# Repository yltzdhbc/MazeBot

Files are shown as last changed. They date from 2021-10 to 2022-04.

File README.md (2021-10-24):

> 📖 本项目更新于 2020 年 08 月 12 日

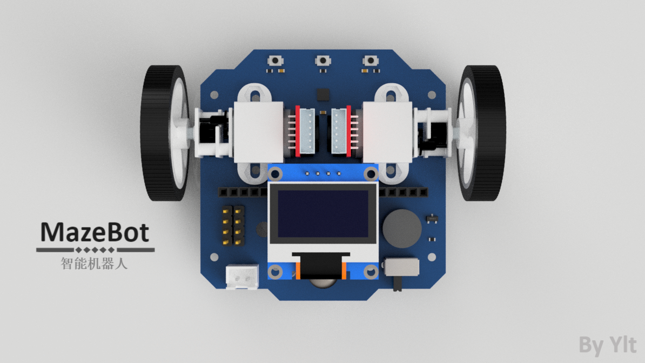
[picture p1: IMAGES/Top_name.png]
Mazebot v1 Top_name


MazeBot 始于2020年四月份，作为一个机器人研究者和爱好者，希望有一个硬件作为载体满足自己的软件的实验。

**我将持续更新该项目的进展**

### MazeBot的硬件资源：

| 元件 | 型号 | 说明 |
| --- | --- | :--- |
| 处理器 | STM32F405RGT6 | 160MHZ主频 DSP浮点加速 |
| 驱动器 | TB6612 | 双路直流电机驱动器 |
| 通讯 | ESP07S | 安信可WiFi芯片 |
| 电机 | N20 | 带正交编码器的直流有刷减速电机 |
| 陀螺仪 | mpu9250 | invensense的9轴姿态传感器 |
| 光电传感器 | ITR8307 | 收发一体的反射式光电传感器 |
| 显示器 | 0.96oled | SSD1306白黑oled |

<!-- more -->

### MazeBot能够用来干什么呢：

- 首先作为一个双轮差速的小车，能够提供最高1m/s的移动速度；
- 通过直流电机编码器反馈与mpu9250陀螺仪信息融合获得可靠的里程计信息；
- 前置五个光电传感器实现巡线学习；
- oled与三个操作按键进行人机交互；
- WiFi与上位机相连获取信息与控制；

---

### 我准备MazeBot做什么：

- 使用OPEN AI 训练其进行巡线；
- 使用模型优化轨迹跟踪算法的参数；

---

### 现在MazeBot完成了哪些部分：

- 电机速度闭环与位置闭环；
- 陀螺仪读取与矫正；
- 基于编码器与陀螺仪的里程计；
- Wifi AP模式和Station模式与上位机通信；
- 光电传感器对白线与黑线的识别；
- 轨迹规划与跟踪算法；

---

### 原理图和PCB

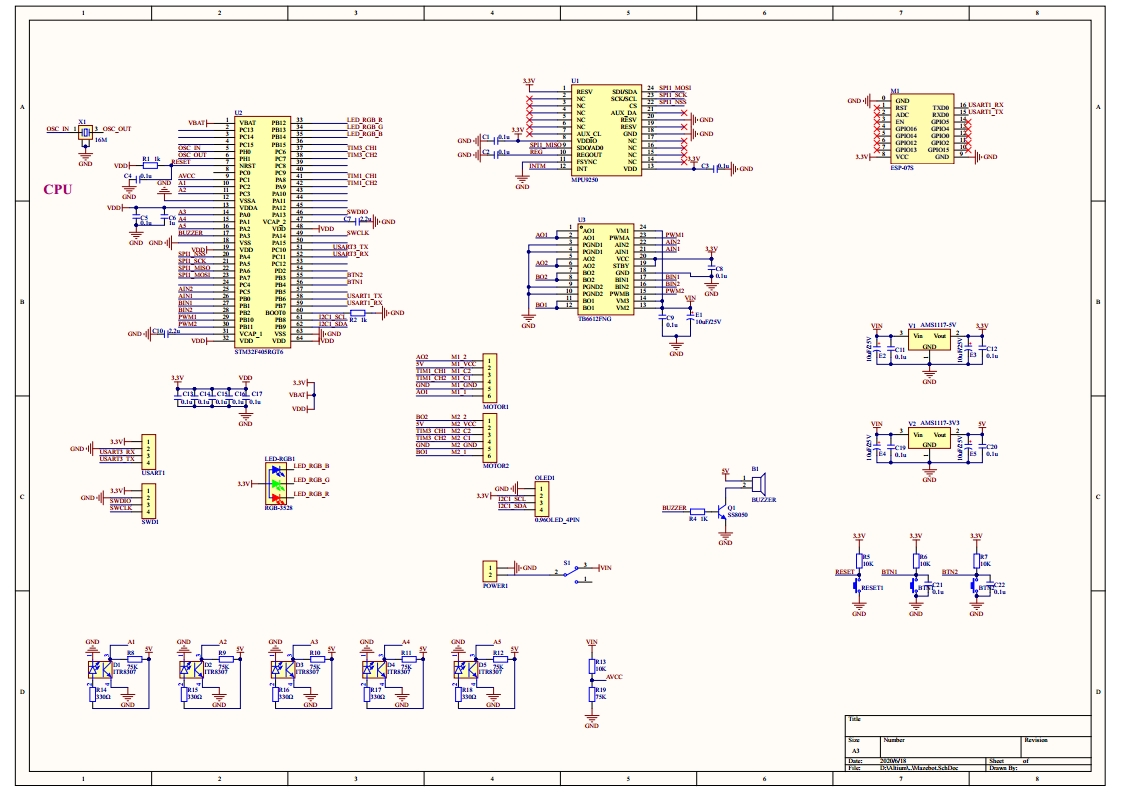
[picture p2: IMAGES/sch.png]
sch


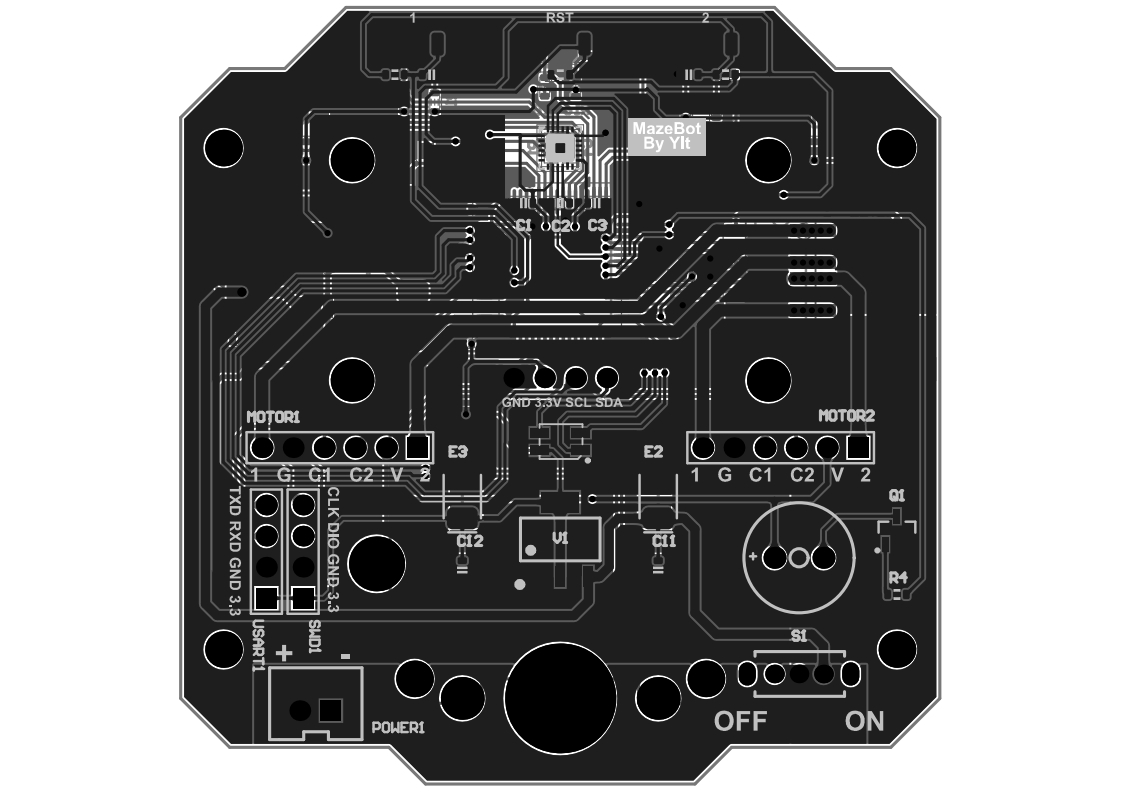
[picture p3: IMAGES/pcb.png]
pcb


### 渲染图

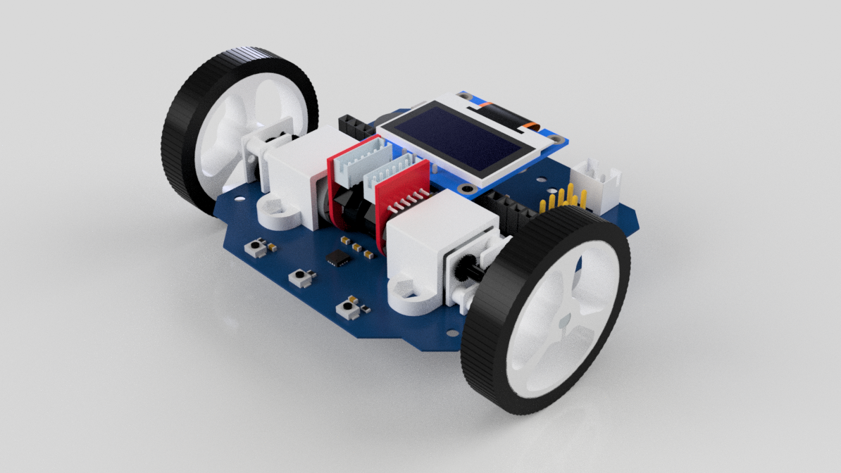
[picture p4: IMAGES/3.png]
Mazebot v2 3


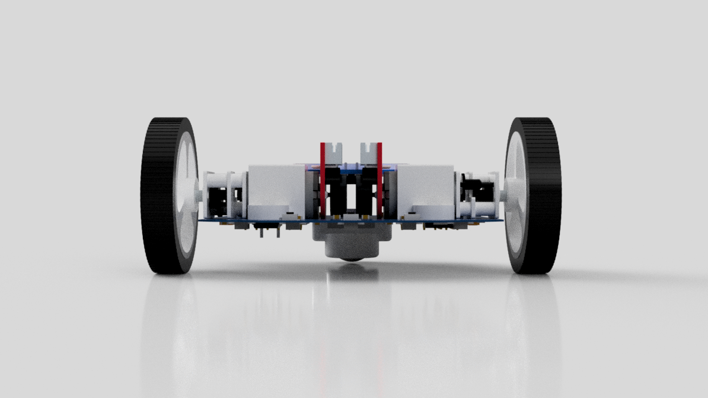
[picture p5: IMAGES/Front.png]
Mazebot v1 Front


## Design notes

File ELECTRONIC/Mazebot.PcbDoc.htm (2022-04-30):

Reporting Options

# File in Previous Format

Date | : | 2022/4/17
Time | : | 14:44:59
Filename | : | C:\UserData\Git\my_github\MazeBot\ELECTRONIC\Mazebot.PcbDoc

Version | Warning

This file was generated by an earlier version of the software

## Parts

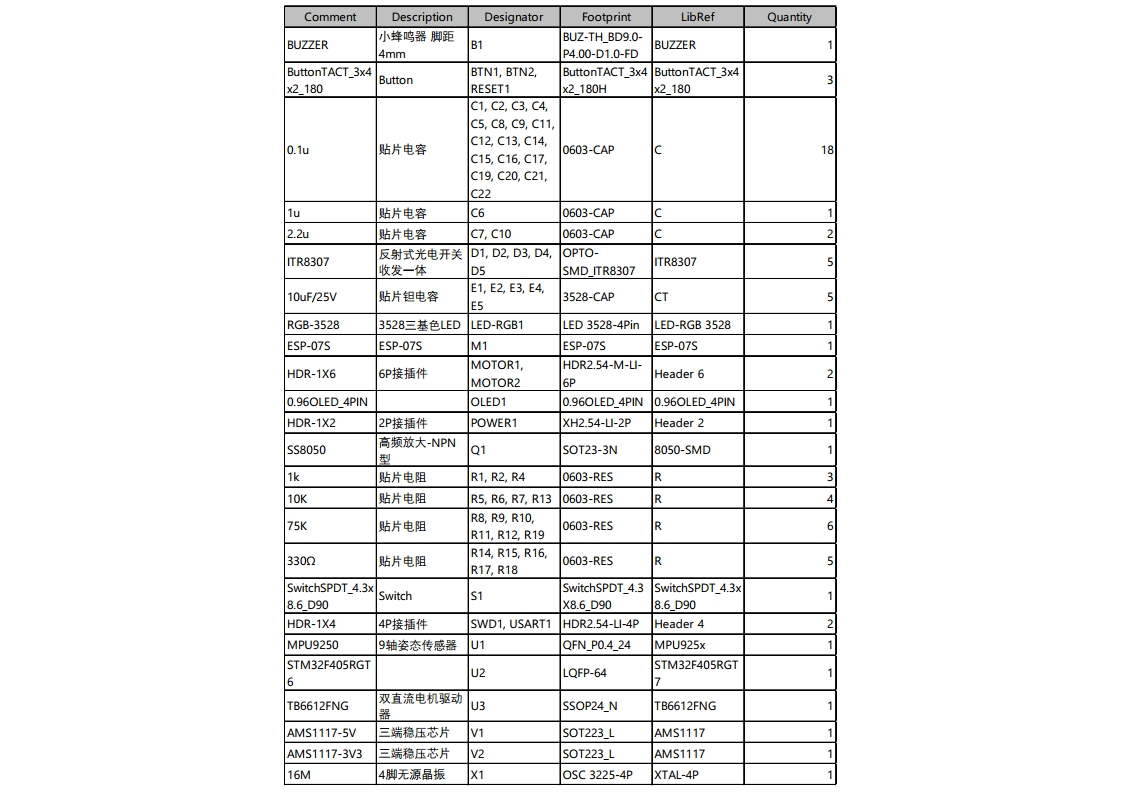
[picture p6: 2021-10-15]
IMAGES/bom.png

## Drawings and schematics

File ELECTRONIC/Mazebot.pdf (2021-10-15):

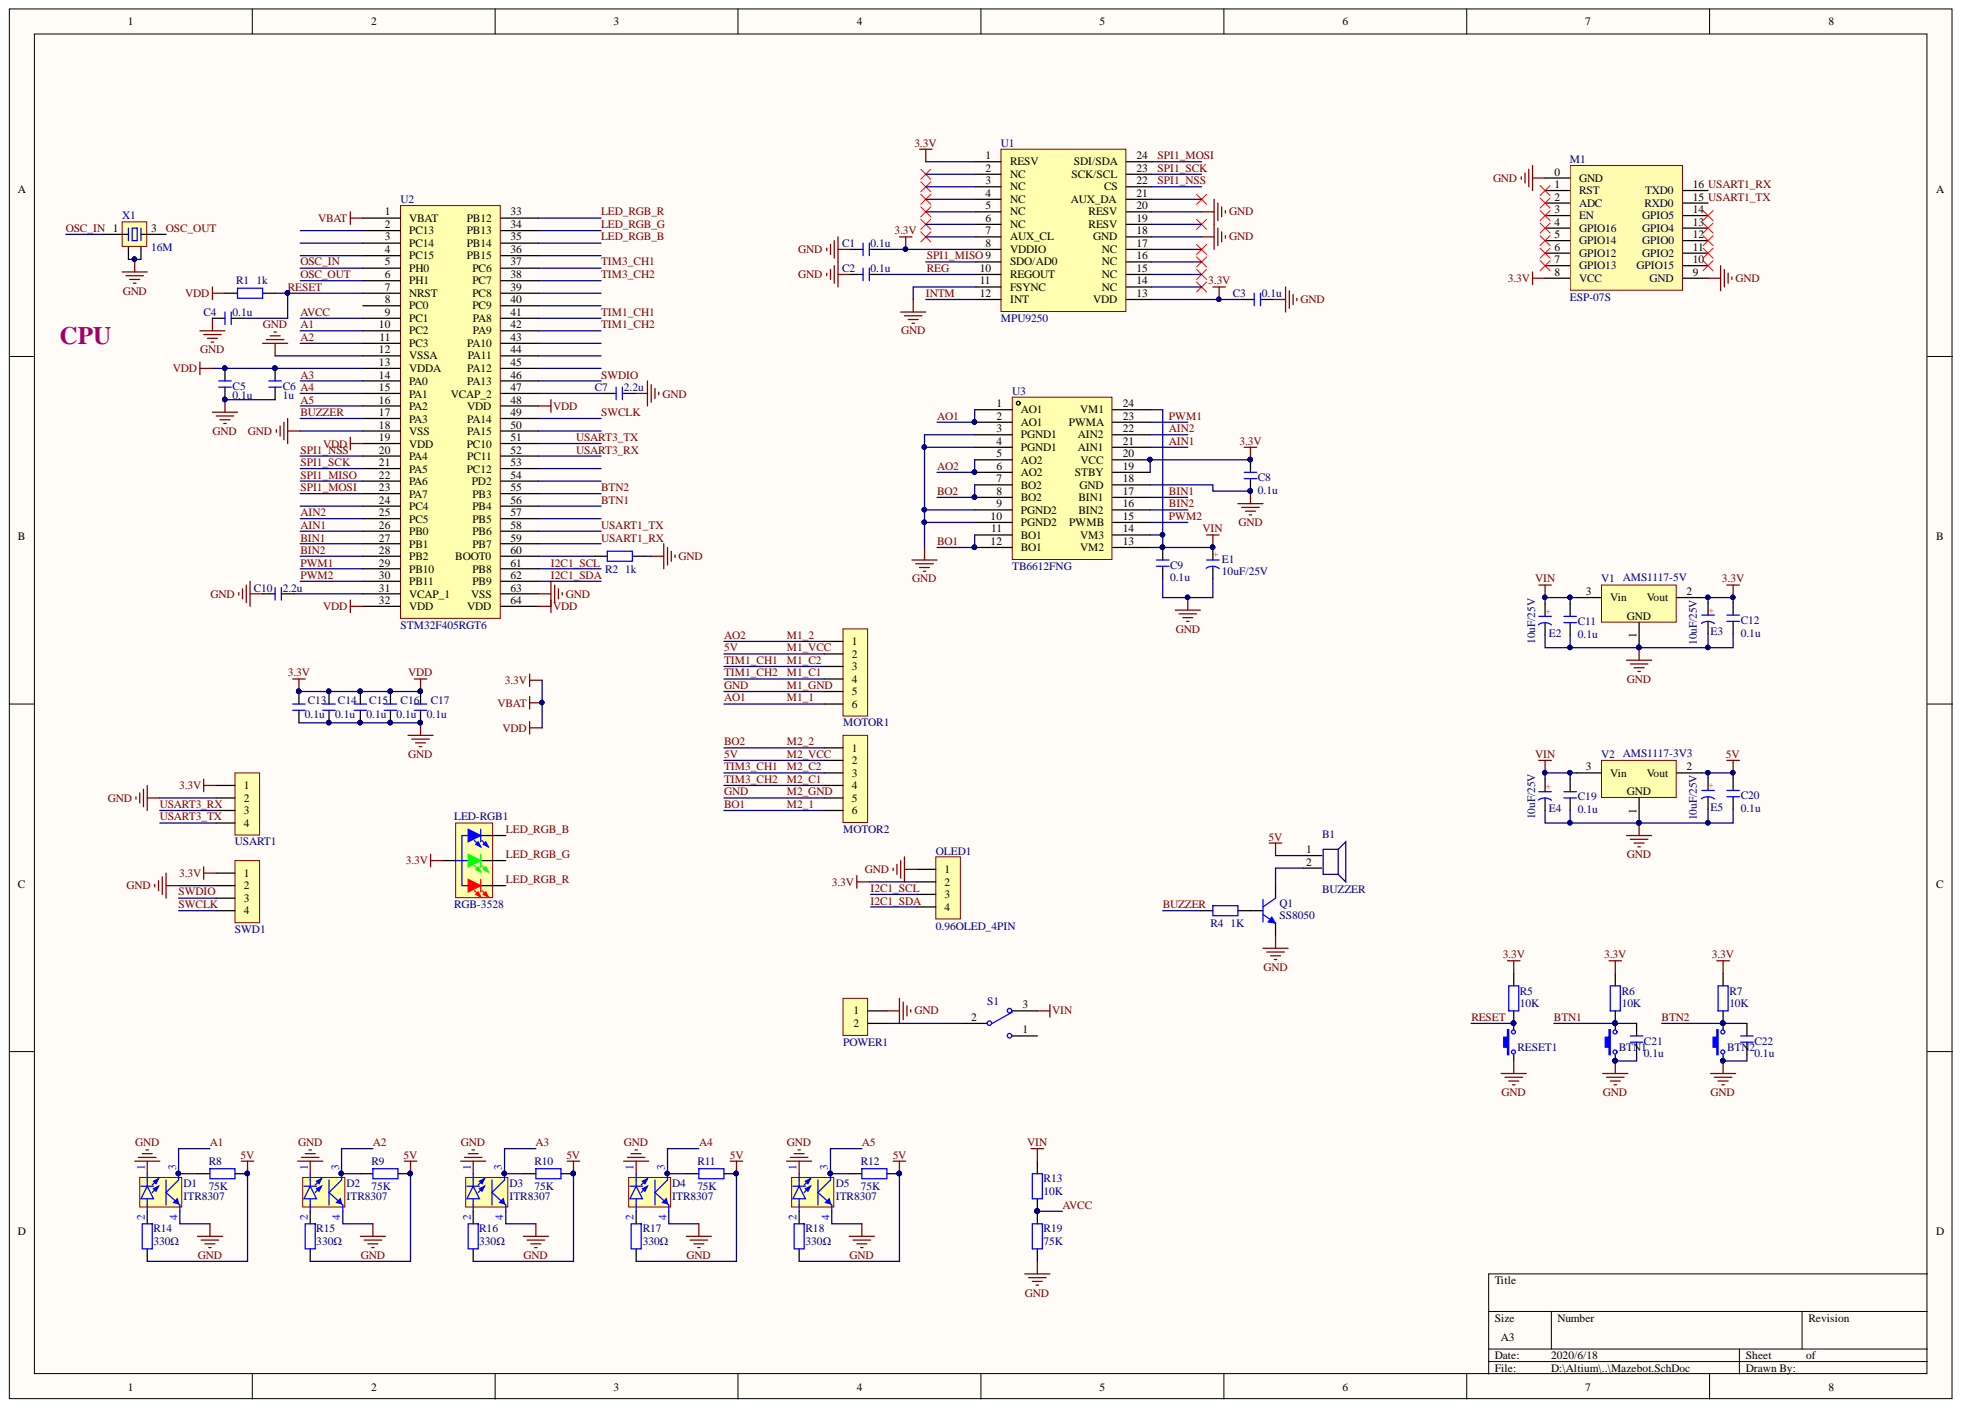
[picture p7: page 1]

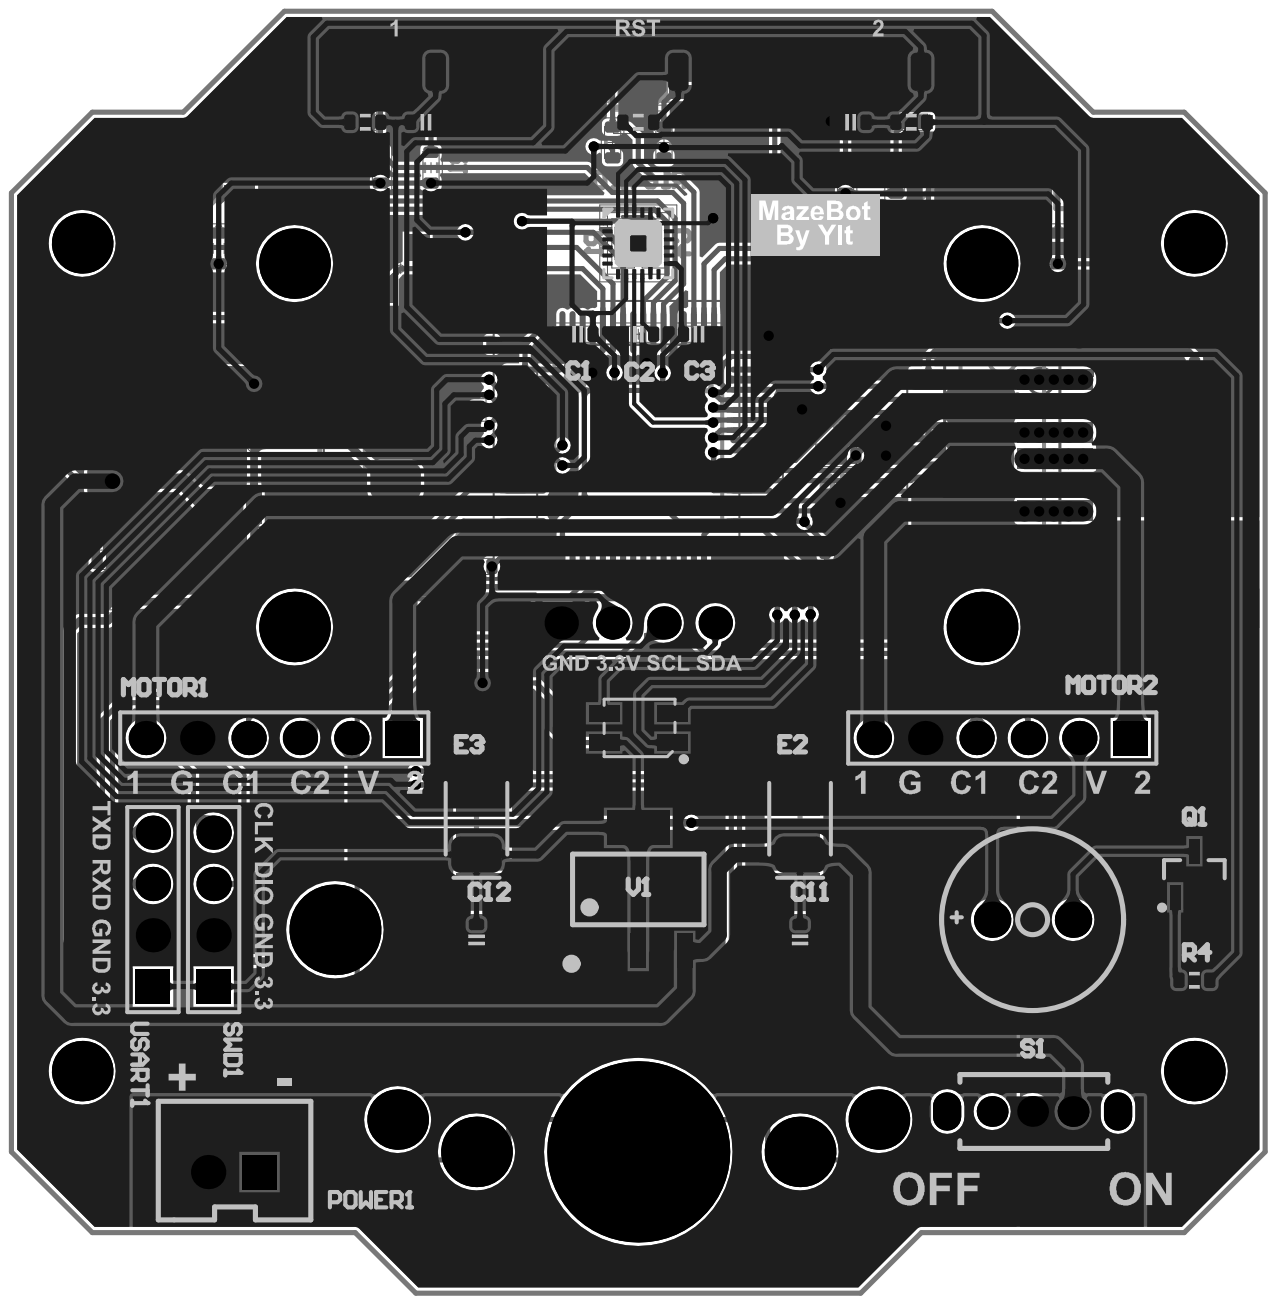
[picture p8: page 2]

Comment | Description | Designator | Footprint | LibRef | Quantity
BUZZER | 小蜂鸣器 脚距 4mm | B1 | BUZ-TH_BD9.0-P4.00-D1.0-FD | BUZZER | 1
ButtonTACT_3x4 x2_180 | Button | BTN1, BTN2, RESET1 | ButtonTACT_3x4 x2_180H | ButtonTACT_3x4 x2_180 | 3
0.1u | 贴片电容 | C1, C2, C3, C4, C5, C8, C9, C11, C12, C13, C14, C15, C16, C17, C19, C20, C21, C22 | 0603-CAP | C | 18
1u | 贴片电容 | C6 | 0603-CAP | C | 1
2.2u | 贴片电容 | C7, C10 | 0603-CAP | C | 2
ITR8307 | 反射式光电开关 收发一体 | D1, D2, D3, D4, D5 | OPTO-SMD_ITR8307 | ITR8307 | 5
10uF/25V | 贴片钽电容 | E1, E2, E3, E4, E5 | 3528-CAP | CT | 5
RGB-3528 | 3528三基色LED | LED-RGB1 | LED 3528-4Pin | LED-RGB 3528 | 1
ESP-07S | ESP-07S | M1 | ESP-07S | ESP-07S | 1
HDR-1X6 | 6P接插件 | MOTOR1, MOTOR2 | HDR2.54-M-LI-6P | Header 6 | 2
0.96OLED_4PIN | | OLED1 | 0.96OLED_4PIN | 0.96OLED_4PIN | 1
HDR-1X2 | 2P接插件 | POWER1 | XH2.54-LI-2P | Header 2 | 1
SS8050 | 高频放大-NPN 型 | Q1 | SOT23-3N | 8050-SMD | 1
1k | 贴片电阻 | R1, R2, R4 | 0603-RES | R | 3
10K | 贴片电阻 | R5, R6, R7, R13 | 0603-RES | R | 4
75K | 贴片电阻 | R8, R9, R10, R11, R12, R19 | 0603-RES | R | 6
330Ω | 贴片电阻 | R14, R15, R16, R17, R18 | 0603-RES | R | 5
SwitchSPDT_4.3x 8.6_D90 | Switch | S1 | SwitchSPDT_4.3 X8.6_D90 | SwitchSPDT_4.3x 8.6_D90 | 1
HDR-1X4 | 4P接插件 | SWD1, USART1 | HDR2.54-LI-4P | Header 4 | 2
MPU9250 | 9轴姿态传感器 | U1 | QFN_P0.4_24 | MPU925x | 1
STM32F405RGT 6 | | U2 | LQFP-64 | STM32F405RGT 7 | 1
TB6612FNG | 双直流电机驱动 器 | U3 | SSOP24_N | TB6612FNG | 1
AMS1117-5V | 三端稳压芯片 | V1 | SOT223_L | AMS1117 | 1
AMS1117-3V3 | 三端稳压芯片 | V2 | SOT223_L | AMS1117 | 1
16M | 4脚无源晶振 | X1 | OSC 3225-4P | XTAL-4P | 1

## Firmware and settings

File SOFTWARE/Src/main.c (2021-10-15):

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

/* Includes ------------------------------------------------------------------*/
#include "main.h"
#include "cmsis_os.h"
#include "adc.h"
#include "i2c.h"
#include "spi.h"
#include "tim.h"
#include "usart.h"
#include "gpio.h"

/* USER CODE BEGIN Includes */
#include "Wifi.h"
#include "WifiConfig.h"
#include "movebase.h"
/* USER CODE END Includes */

/* USER CODE BEGIN PD */
//typedef union _adc_data
//{
//  uint8_t data[16];
//  float ActVal[4];
//} adcdata_def;
/* USER CODE END PD */


/* USER CODE BEGIN PV */
//float ADC_Value_Temp[6];
//adcdata_def ADC_Value;
/* USER CODE END PV */

void SystemClock_Config(void);
void MX_FREERTOS_Init(void);
/**
  * @brief  The application entry point.
  * @retval int
  */
int main(void)
{
  

  /* MCU Configuration--------------------------------------------------------*/

  /* Reset of all peripherals, Initializes the Flash interface and the Systick. */
  HAL_Init();

  /* Configure the system clock */
  SystemClock_Config();

  /* Initialize all configured peripherals */
  MX_GPIO_Init();
  MX_ADC1_Init();
  MX_I2C1_Init();
  MX_SPI1_Init();
  MX_TIM1_Init();
  MX_TIM2_Init();
  MX_TIM3_Init();
  MX_USART3_UART_Init();
  MX_TIM6_Init();
  MX_TIM5_Init();
  MX_USART1_UART_Init();
  /* USER CODE BEGIN 2 */
  printf("*** MazeBot Init! *** \r\n");

  HAL_TIM_Encoder_Start(&MOTOR0_TIM, TIM_CHANNEL_ALL);
  HAL_TIM_Encoder_Start(&MOTOR1_TIM, TIM_CHANNEL_ALL);

  HAL_TIM_PWM_Start(&MOTOR_PWM_TIM, MOTOR0_PWM_TIM_CHANNEL);
  HAL_TIM_PWM_Start(&MOTOR_PWM_TIM, MOTOR1_PWM_TIM_CHANNEL);
	
	//HAL_ADCEx_Calibration_Start(&hadc1); //ADC校准
	
	//开启ADC DMA传输 400个数据一个循环，一路采集100个数据，做滤波
//  HAL_ADC_Start_DMA(&hadc1, (uint32_t*)&ADC_Value_Temp, 60);

  //	HAL_TIM_PWM_Start(&BUZZER_TIM, BUZZER_TIM_CHANNEL);
  //
  //	__HAL_TIM_SET_AUTORELOAD(&BUZZER_TIM, 2000);

  //	__HAL_TIM_SET_COMPARE(&BUZZER_TIM, BUZZER_TIM_CHANNEL, 1000);

  /* USER CODE END 2 */

  /* Call init function for freertos objects (in freertos.c) */
  MX_FREERTOS_Init(); 

  /* Start scheduler */
  osKernelStart();
  
  /* We should never get here as control is now taken by the scheduler */

  /* Infinite loop */
  /* USER CODE BEGIN WHILE */
  while (1)
  {

    /* USER CODE END WHILE */

    /* USER CODE BEGIN 3 */
  }
  /* USER CODE END 3 */
}

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
/**
  * @brief  Period elapsed callback in non blocking mode
  * @note   This function is called  when TIM10 interrupt took place, inside
  * HAL_TIM_IRQHandler(). It makes a direct call to HAL_IncTick() to increment
  * a global variable "uwTick" used as application time base.
  * @param  htim : TIM handle
  * @retval None
  */
void HAL_TIM_PeriodElapsedCallback(TIM_HandleTypeDef *htim)
{
  if (htim->Instance == TIM10) {
    HAL_IncTick();
  }
}

/**
  * @brief  This function is executed in case of error occurrence.
  * @retval None
  */
void Error_Handler(void)
{
  /* USER CODE BEGIN Error_Handler_Debug */
  /* User can add his own implementation to report the HAL error return state */

  /* USER CODE END Error_Handler_Debug */
}

#ifdef  USE_FULL_ASSERT
/**
  * @brief  Reports the name of the source file and the source line number
  *         where the assert_param error has occurred.
  * @param  file: pointer to the source file name
  * @param  line: assert_param error line source number
  * @retval None
  */
void assert_failed(uint8_t *file, uint32_t line)
{ 
  /* USER CODE BEGIN 6 */
  /* User can add his own implementation to report the file name and line number,
     tex: printf("Wrong parameters value: file %s on line %d\r\n", file, line) */
  /* USER CODE END 6 */
}
#endif /* USE_FULL_ASSERT */

/************************ (C) COPYRIGHT STMicroelectronics *****END OF FILE****/

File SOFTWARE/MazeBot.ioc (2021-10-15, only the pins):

Mcu.UserName=STM32F405RGTx
PA0-WKUP.Signal=ADCx_IN0
PA1.Signal=ADCx_IN1
PA13.Signal=SYS_JTMS-SWDIO
PA14.Signal=SYS_JTCK-SWCLK
PA2.Signal=ADCx_IN2
PA3.GPIO_Label=BUZZER
PA3.Signal=S_TIM5_CH4
PA4.Signal=SPI1_NSS
PA5.Signal=SPI1_SCK
PA6.Signal=SPI1_MISO
PA7.Signal=SPI1_MOSI
PA8.Signal=S_TIM1_CH1
PA9.Signal=S_TIM1_CH2
PB0.GPIO_Label=AIN1
PB0.Signal=GPIO_Output
PB1.GPIO_Label=BIN1
PB1.Signal=GPIO_Output
PB10.GPIO_Label=PWM1
PB10.Signal=S_TIM2_CH3
PB11.GPIO_Label=PWM2
PB11.Signal=S_TIM2_CH4
PB12.GPIO_Label=LED_RGB_R
PB12.Signal=GPIO_Output
PB13.GPIO_Label=LED_RGB_G
PB13.Signal=GPIO_Output
PB14.GPIO_Label=LED_RGB_B
PB14.Signal=GPIO_Output
PB2.GPIO_Label=BIN2
PB2.Signal=GPIO_Output
PB3.GPIO_Label=BTN2
PB3.Signal=GPXTI3
PB4.GPIO_Label=BTN1
PB4.Signal=GPXTI4
PB6.Signal=USART1_TX
PB7.Signal=USART1_RX
PB8.Signal=I2C1_SCL
PB9.Signal=I2C1_SDA
PC1.Signal=ADCx_IN11
PC10.Signal=USART3_TX
PC11.Signal=USART3_RX
PC2.Signal=ADCx_IN12
PC3.Signal=ADCx_IN13
PC5.GPIO_Label=AIN2
PC5.Signal=GPIO_Output
PC6.Signal=S_TIM3_CH1
PC7.Signal=S_TIM3_CH2
PH0-OSC_IN.Signal=RCC_OSC_IN
PH1-OSC_OUT.Signal=RCC_OSC_OUT

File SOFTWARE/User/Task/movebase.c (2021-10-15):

#include <math.h>
#include <stdio.h>
#include "main.h"
#include "tim.h"
#include "usart.h"
#include "bsp_usart.h"
#include "bsp_led.h"
#include "movebase.h"
#include "cmsis_os.h"

#define MOTOR_NUM 2
#define TICK2ANGLE 0.42857f     //脉冲与角度的转换系数
#define RPM2MPS 0.00178023f     // 2PIR/60  R=0.017
#define MPS2RPM 561.723338f     // 60/2PIR  R=0.017

#define TICK2RAD 0.00747998238f //TICK*2PI/840 = RAD
#define WHEEL_SEPARATION 0.087f //左右轮间距
#define WHEEL_RADIUS 0.017f     //轮子半径

Odom_t Odom;
MotorType Motor[MOTOR_NUM];
DriverType Driver[MOTOR_NUM] = {0};
float PerPwm[MOTOR_NUM] = {0};

//*****************      m/s          m/s         rad/s
void Output_Wheel(float vel_x, float vel_y, float w_z)
{
  float Vel_l, Vel_r;

  Vel_l = vel_y - w_z * WHEEL_SEPARATION / 2;
  Vel_r = vel_y + w_z * WHEEL_SEPARATION / 2;

  Driver[0].velCtrl.desiredVel[CMD] = Vel_l * MPS2RPM;
  Driver[1].velCtrl.desiredVel[CMD] = Vel_r * MPS2RPM;
}

extern float ADC_Value_Temp[6];

#include "adc.h"
uint16_t ADC_Value;

void ChassisTask(void const *argument)
{

  uint32_t time_now, prev_time, d_time;
  DriverInit(); //驱动器初始化

  for (;;)
  {
//	  HAL_ADC_Start(&hadc1);
//    HAL_ADC_PollForConversion(&hadc1, 50);
// 
//    if(HAL_IS_BIT_SET(HAL_ADC_GetState(&hadc1), HAL_ADC_STATE_REG_EOC))
//    {
//      ADC_Value = HAL_ADC_GetValue(&hadc1);
//      printf("ADC Reading : %d \r\n",ADC_Value);
//		}
		//printf("%f , %f , %f , %f , %f , %f\r\n",ADC_Value_Temp[0],ADC_Value_Temp[1],ADC_Value_Temp[2],ADC_Value_Temp[3],ADC_Value_Temp[4],ADC_Value_Temp[5]);
    /*获取当前时间 计算周期时间差 记录*/
    time_now = HAL_GetTick();
    d_time = time_now - prev_time;
    prev_time = time_now;

    /*读取编码器信息 获得反馈 速度、位置*/
    UpdataEncoderInfo(&Motor[0], 65535 - __HAL_TIM_GET_COUNTER(&MOTOR0_TIM), d_time);
    UpdataEncoderInfo(&Motor[1], __HAL_TIM_GET_COUNTER(&MOTOR1_TIM), d_time);

    MotorCtrl(); //电机控制

    calcOdometry(&Odom, d_time); //计算里程计

    osDelay(10);
  }
}

void calcOdometry(Odom_t *Odom, uint32_t diff_time)
{
  float wheel_l, wheel_r; // 运动弧长 [rad]
  float delta_s, delta_theta;
  float step_time;

  step_time = diff_time / 1000.0f; //MS转换为S
  if (step_time == 0)
    return;

  wheel_l = (float)Motor[0].total_tick_diff * TICK2RAD * WHEEL_RADIUS; //左轮运动弧长 m
  wheel_r = (float)Motor[1].total_tick_diff * TICK2RAD * WHEEL_RADIUS; //又轮运动弧长 m

  delta_s = (wheel_l + wheel_r) / 2;                    //计算单位弧长
  delta_theta = (wheel_r - wheel_l) / WHEEL_SEPARATION; //计算偏转角

  Odom->Pos.theta += delta_theta;
  Odom->Pos.y += delta_s * cos(Odom->Pos.theta);
  Odom->Pos.x -= delta_s * sin(Odom->Pos.theta);

  Odom->Vel.wz = (Motor[1].vel - Motor[0].vel) * RPM2MPS / WHEEL_SEPARATION;
  Odom->Vel.vy = (Motor[1].vel + Motor[0].vel) * RPM2MPS / 2;
  Odom->Vel.vx = 0.0f;
}

/**
  * @brief  电机控制函数
  * @brief  放在定时器定时中断回调函数中 使用中断运行
	* @param  None
	* @retval None
  */
void MotorCtrl(void)
{
  for (int i = 0; i < MOTOR_NUM; i++)
  {
    if (Motor[i].type == NONE)
      break;

    /*计算最后的期望位置 有位置判断 防溢出*/
    CalculSpeed_Pos(&Driver[i], &Motor[i]);

    if (Driver[i].status != ENABLE)
    {
      Driver[i].output = 0.0f;
      continue;
    }

    /*驱动器模式选择状态机*/
    switch (Driver[i].unitMode)
    {
    case POSITION_CONTROL_MODE: //位置控制
      /*进行位置环计算 输入期望位置 输入反馈位置 输出速度控制量*/
      PosCtrl(&Driver[i].posCtrl);
      /*将位置环的输出传递给速度环的期望速度*/
      Driver[i].velCtrl.desiredVel[CMD] = Driver[i].posCtrl.output;
      /*速度斜坡输入 */
      VelSlope(&Driver[i].velCtrl);
      /*进行速度环计算 输入期望速度 输入反馈速度 输出电流环控制量*/
      Driver[i].output = VelPidCtrl(&Driver[i].velCtrl);
      break;
    case SPEED_CONTROL_MODE: //速度控制
      /*速度斜坡输入*/
      VelSlope(&Driver[i].velCtrl);
      /*进行速度环计算 输入期望速度 输入反馈速度 输出电流环控制量*/
      Driver[i].output = VelPidCtrl(&Driver[i].velCtrl);
      break;
    case HOMING_MODE:
      HomingMode(&Driver[i]); //零点校准
      Driver[i].output = Driver[i].homingMode.output;
      break;
    default:
      break;
    }
  }

  /*驱动输出控制量给到驱动器控制电机*/
  for (int i = 0; i < MOTOR_NUM; i++)
  {
    if (Motor[i].type == DC_MOTOR)
    {
      PerPwm[i] = Driver[i].output * 1.0f;
    }
    else
      PerPwm[i] = 0.0f;
  }

  /*设定电机Pwm值*/
  SetPwmMotor0(PerPwm[0]);
  SetPwmMotor1(PerPwm[1]);
}

/**
  * @brief  驱动器初始化
  * @param  None
  * @retval 在main.c中初始调用
  */
void DriverInit(void)
{
  Driver[0].command.Id = 0;
  Driver[1].command.Id = 1;
  Motor[0].type = DC_MOTOR;
  Motor[1].type = DC_MOTOR;

  for (int i = 0; i < MOTOR_NUM; i++)
  {
    Driver[i].status = ENABLE;        //驱动状态
    Driver[i].encoder.period = 65535; //编码器溢出值

    if (Motor[i].type == DC_MOTOR)
    {
      Driver[i].unitMode = SPEED_CONTROL_MODE;
      Driver[i].velCtrl.kp = VEL_KP_DC;
      Driver[i].velCtrl.ki = VEL_KI_DC;
      Driver[i].velCtrl.maxOutput = CURRENT_MAX_DC;
      Driver[i].velCtrl.desiredVel[MAX_V] = VEL_MAX_DC;
      Driver[i].posCtrl.kd = POS_KD_DC;
      Driver[i].posCtrl.kp = POS_KP_DC;
      Driver[i].homingMode.current = 0.8f;
      Driver[i].velCtrl.acc = 50.0f;
      Driver[i].velCtrl.dec = 50.0f;
      Driver[i].velCtrl.desiredVel[CMD] = 0.0f;
      Driver[i].posCtrl.acc = Driver[i].velCtrl.dec;
      Driver[i].posCtrl.posVel = 50.0f;
      Driver[i].homingMode.vel = -160.0f;
    }
    else
    {
      break;
    }
  }
}

/**
  * @brief  更新编码器输入脉冲信息
  * @param  None
  * @retval tick是编码器返回的脉冲数值 范围为0-65536
  *         last_tick记录上一个周期的脉冲值 判断脉冲是否溢出
  */
void UpdataEncoderInfo(MotorType *Motor, uint16_t tick, uint32_t d_time)
{
  //判断编码器脉冲计数溢出
  if ((int32_t)(tick - Motor->last_tick) > 32768)
    Motor->round_cnt--;
  else if ((int32_t)(tick - Motor->last_tick) < -32768)
    Motor->round_cnt++;
  //保存本周期的脉冲
  Motor->last_tick = tick;
  //计算编码器的绝对脉冲
  Motor->total_tick = Motor->round_cnt * 65536 + tick;
  //计算绝对脉冲的差值
  Motor->total_tick_diff = Motor->total_tick - Motor->last_total_tick;
  //保存本周期的绝对脉冲值
  Motor->last_total_tick = Motor->total_tick;
  //计算总转角 度
  Motor->pos = Motor->total_tick * TICK2ANGLE;
  // //一个周期的角 度
  // Motor->pos_diff = Motor->pos - Motor->last_pos;
  // Motor->last_pos = Motor->pos;
  //计算速度 RPM
  Motor->vel = (Motor->total_tick_diff / 840.0f) * (60000.0f / d_time);
}
/**
  * @brief  设定电机1 Pwm值 控制电机速度
  * @param  输入Pwm值
  * @retval none
  */
void SetPwmMotor0(float PwmInput)
{
  float PwmOutput;
  if (PwmInput == 0)
  {
    PwmOutput = 0;
    HAL_GPIO_WritePin(AIN1_GPIO_Port, AIN1_Pin, GPIO_PIN_RESET);
    HAL_GPIO_WritePin(AIN2_GPIO_Port, AIN2_Pin, GPIO_PIN_RESET);
  }
  else if (PwmInput > 0)
  {
    PwmOutput = PwmInput;
    HAL_GPIO_WritePin(AIN1_GPIO_Port, AIN1_Pin, GPIO_PIN_RESET);
    HAL_GPIO_WritePin(AIN2_GPIO_Port, AIN2_Pin, GPIO_PIN_SET);
  }
  else
  {
    PwmOutput = -PwmInput;
    HAL_GPIO_WritePin(AIN1_GPIO_Port, AIN1_Pin, GPIO_PIN_SET);
    HAL_GPIO_WritePin(AIN2_GPIO_Port, AIN2_Pin, GPIO_PIN_RESET);
  }

  __HAL_TIM_SET_COMPARE(&MOTOR_PWM_TIM, MOTOR0_PWM_TIM_CHANNEL, PwmOutput);
}
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

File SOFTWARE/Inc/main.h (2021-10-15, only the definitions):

#define BUZZER_Pin GPIO_PIN_3
#define BUZZER_GPIO_Port GPIOA
#define AIN2_Pin GPIO_PIN_5
#define AIN2_GPIO_Port GPIOC
#define AIN1_Pin GPIO_PIN_0
#define AIN1_GPIO_Port GPIOB
#define BIN1_Pin GPIO_PIN_1
#define BIN1_GPIO_Port GPIOB
#define BIN2_Pin GPIO_PIN_2
#define BIN2_GPIO_Port GPIOB
#define PWM1_Pin GPIO_PIN_10
#define PWM1_GPIO_Port GPIOB
#define PWM2_Pin GPIO_PIN_11
#define PWM2_GPIO_Port GPIOB
#define LED_RGB_R_Pin GPIO_PIN_12
#define LED_RGB_R_GPIO_Port GPIOB
#define LED_RGB_G_Pin GPIO_PIN_13
#define LED_RGB_G_GPIO_Port GPIOB
#define LED_RGB_B_Pin GPIO_PIN_14
#define LED_RGB_B_GPIO_Port GPIOB
#define BTN2_Pin GPIO_PIN_3
#define BTN2_GPIO_Port GPIOB
#define BTN1_Pin GPIO_PIN_4
#define BTN1_GPIO_Port GPIOB
#define SPI_NSS_Pin GPIO_PIN_4
#define SPI_NSS_GPIO_Port GPIOA
#define MOTOR0_TIM htim1
#define MOTOR1_TIM htim3
#define MOTOR_PWM_TIM htim2
#define MOTOR0_PWM_TIM_CHANNEL TIM_CHANNEL_3
#define MOTOR1_PWM_TIM_CHANNEL TIM_CHANNEL_4
#define BUZZER_TIM htim5
#define BUZZER_TIM_CHANNEL TIM_CHANNEL_4

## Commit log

2021-10-15 提交Git
    [MazeBot.PrjPCB, Mazebot.SchDoc]
2021-10-24 更新README
2021-10-24 更新描述
2021-12-06 更新工程框架
2022-04-30 删除room

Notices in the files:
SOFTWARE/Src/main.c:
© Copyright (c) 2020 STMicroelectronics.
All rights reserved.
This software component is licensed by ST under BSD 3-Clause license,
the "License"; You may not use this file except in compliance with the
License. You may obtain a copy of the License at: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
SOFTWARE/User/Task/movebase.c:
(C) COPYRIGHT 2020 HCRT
